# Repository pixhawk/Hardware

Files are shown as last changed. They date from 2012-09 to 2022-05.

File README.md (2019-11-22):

# Pixhawk Hardware Designs

 

[Pixhawk](http://pixhawk.org) is an independent open-hardware project that aims to provide "the gold standard" for readily-available, hiqh-quality and low-cost autopilot hardware designs for the academic, hobby and developer communities.
Pixhawk supports multiple flight stacks: PX4 ® and ArduPilot ®.

> **Note** Designs are provided for a number of components used in unmanned vehicles, including: Autopilots (Flight Management Units - FMUs), ESCs (electronic speed controllers), optical flow sensors, etc.

## What are Open Hardware Designs?

The [Pixhawk project](https://pixhawk.org/) provides open hardware designs following the [OSHW 1.1 definition](https://www.oshwa.org/definition/).

In essence, this definition allows anyone to freely study, modify, distribute, make, and sell the designs (or hardware based on the designs) under the terms of a particular [open source licence](#licensing).

## Hardware Designs

Hardware designs delivered by the project are listed below.

<span id="fmu_designs"></span>
### FMU (Autopilot) Designs

Pixhawk FMU open designs include all information required to create an autopilot hardware product that is *firmware compatible* with other hardware created from the same design.
Manufacturers are encouraged to take the designs and create products that are best suited to a particular market or use case (e.g. for very small vehicles, or those that operate at environmental extremes).

> **Note** While a physical connector standard is not mandated, newer products generally follow the [Pixhawk Connector Standard](https://pixhawk.org/pixhawk-connector-standard/).

#### Design Specifications

Designs are *usually* specified in the form of *schematics* that show all included components (CPU, sensors, etc.), how they are connected, and their pin mappings.
They may also include a BOM (bill of materials).

> **Note** Not all designs deliver schematics.
  A minimal design needs to contain enough information for manufacturers to create a compatible products; this can also be achieved using a precise pinout definition and information about connections of internal/external busses, etc.

#### Open Reference Hardware

The project provides *open reference hardware/layouts* for **some** open designs, in some versions.
These are provided in the form of PCB layout files.

The reference hardware files are shared under the same [license](#licenses) as the associated open design, and hence may be used in the same way(s).

#### FMU Versions

The Pixhawk project has evolved the FMU design through a number of verisons.

These are named using the designation: FMUvX (e.g.: FMUv1, FMUv2, FMUv3, FMUv4, etc.).
Higher FMU numbers indicate that the board is more recent, but may not indicate increased capability (versions can be almost identical - differing only in connector wiring).

The versions are listed below (with a high level overview of the main differences).

Version | Year | Lead Product | CPU | Other
--- | --- | --- | --- | ---
[FMUv1](FMUv1/README.md) & [IOv1](IOv1) | 2012 | None | 168 MHz M4 | (Discontinued) Original Flight Management Unit and Separate I/O board.
[FMUv2](FMUv2/README.md) | 2013 | Pixhawk 1 | 168 MHz M4 | Single board with STM32427VI processor.
[FMUv3](FMUv3_REV_D/README.md) | 2015 | Pixhawk 2 | 168 MHz M4 | Redundant sensors. Identical to FMUv2, but usable flash doubled to 2MB.
[FMUv4](FMUv4/README.md) | 2015 | Pixracer | 168 MHz M4 | Increased RAM. Faster CPU. More serial ports. No IO processor.
FMUv4X | 2017 | Pixhawk 3 Pro | 168 MHz M4 | Slightly increased RAM. More serial ports. IO processor. Redundant sensors.
[FMUv5](FMUv5/README.md) | 2018 | Pixhawk 4 | 200 MHz M7 | New processor (F7). Much faster. More RAM. More CAN busses. Much more configurable.<br>> **Note** Minimum specification provided (pinout info, but no schematics).
FMUv5X | 2019 | Pixhawk 5X | 200 MHz M7 | Temp-calibrated, redundant sensors.

> **Note** Products based on Pixhawk designs are listed here: [PX4 User Guide > Pixhawk Series]( https://docs.px4.io/master/en/flight_controller/pixhawk_series.html#pixhawk-series).

#### Derived FMU Products

Commercial products that are *derived* (under the terms of the open source license) from the Pixhawk FMU designs must provide their schematics and other information.

Relevant products are listed below:

- [MindPX V2 Hardware](MindPXv2/README.md)

### Sapog ESC

- [Sapog ESC](https://github.com/PX4/sapog) Hardware - The directory [sapog_reference_hardware](sapog_reference_hardware/README.md) contains the reference hardware design for the Sapog ESC firmware.

### Other

- [AIRSPEEDv1](AIRSPEEDv1) - 
- [FLOWv1](FLOWv1)
- [IMUv3_REV_C](IMUv3_REV_C)
- [PSMv3_REV_C](PSMv3_REV_C)

<span id="dev_call"></span>
## Dev Call

Pixhawk standards are developed in a weekly public developer call.

The call is shown in the [Dronecode calendar](https://www.dronecode.org/calendar/) as: *Pixhawk Hardware Standards Weekly Call* (all call details are in the entry).

<span id="licensing"></span>
## Licensing and Trademarks

Pixhawk project schematics and reference designs are licensed under [CC BY-SA 3](https://creativecommons.org/licenses/by-sa/3.0/legalcode).

The license allows you to use, sell, share, modify and build on the files in almost any way you like - provided that you give credit/attribution, and that you share any changes that you make under the same open source license (see the [human readable version of the license](https://creativecommons.org/licenses/by-sa/3.0/) for a concise summary of the rights and obligations).

> **Note** Boards that are *derived directly* from Pixhawk schematic files (or reference boards) must be open sourced.
  They can't be commercially licensed as proprietary products.

Manufacturers can create (compatible) *fully independent products* by first generating fresh schematic files that have the same pin mapping/components as the FMU designs.
Products that are based on independently created schematics are considered original works, and can be licensed as required.

<span id="trademarks"></span>
## Trademarks

The term *Pixhawk* is a trademark, and may not be used in product names without explicit permission from the trademark owner.

Typically this trademark is granted to the first board based on a particular FMU design and/or boards that use Pixhawk open reference hardware layouts.

> **Note** A "Pixhawk" is an autopilot that has been been given permission to use the Pixhawk trademark in its name.
  While other boards are based on the "Pixhawk FMU Standard", the are not *strictly speaking* "Pixhawks".

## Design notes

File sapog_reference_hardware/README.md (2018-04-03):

# Reference Hardware for PX4 Sapog



This directory contains the reference hardware design for
[PX4 Sapog](https://kb.zubax.com/x/cYAh) - an advanced open source ESC firmware.

This specific design is intended as an application note;
the main knowledge to gather from this design is the pinout of the MCU and its immediate connections.
The design is implemented in Eagle, version 7 or newer is required.

## Resources

* **[HOMEPAGE](https://kb.zubax.com/x/cYAh)**
* **[SUPPORT & FEEDBACK](https://forum.zubax.com/)**
* **[FIRMWARE ON GITHUB](https://github.com/PX4/sapog)**

## Design guidelines

1. When choosing the power transistors, keep their dynamic characteristics in mind:
the switching time must be under 50 nanoseconds.
Sapog employs somewhat unorthodox methods of state estimation which require a high-speed inverter.
2. The RC filters in the phase voltage feedback circuits should be designed so that their cutoff frequency
is around 19 kHz and the output impedance does not exceed 8 kohm.
3. Unless your maximum supply voltage exceeds 25 V (6S), do not change the DC link voltage measurement divider.

## License

The design is distributed under the terms of the
Creative Commons Attribution-ShareAlike 3.0 Unported license (CC BY-SA 3.0).

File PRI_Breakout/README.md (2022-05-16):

# Pixhawk Radio Interface (PRI) Breakout Board

> **General information about Pixhawk designs, schematics, reference hardware, FMU versions, licensing, and trademarks, and contributing to the project can be found in the repo [README](../README.md).**

This folder contains the design files for the PRI breakout board which splits the PRI connector into a power in, ethernet, usb and serial port. Documentation about the PRI standard can be found [here](https://github.com/pixhawk/Pixhawk-Standards).

## Design Files

The design is provided in [Altium Designer](https://www.altium.com/) CAD files.

It consists of schematic files (*.SchDoc), BOM listings, and includes open reference hardware PCB layouts (.PrjPcb). 

> **Tip** PDF versions of the schematics and PCB layouts has been made available for easy previewing (i.e. if you don't have Altium Designer).

<span id="licensing"></span>
## Licensing and Trademarks

The PRI breakout board design files are contributed by Auterion AG and licensed under [CC BY-SA 3](https://creativecommons.org/licenses/by-sa/3.0/legalcode).

The license allows you to use, sell, share, modify and build on the files in almost any way you like - provided that you give credit/attribution, and that you share any changes that you make under the same open source license (see the [human readable version of the license](https://creativecommons.org/licenses/by-sa/3.0/) for a concise summary of the rights and obligations).

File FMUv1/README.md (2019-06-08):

# FMUv1 Pixhawk Open Hardware Design

> **General information about Pixhawk designs, schematics, reference hardware, FMU versions, licensing, and trademarks, and contributing to the project can be found in the repo [README](../README.md).**

This is the first Pixhawk FMU design, and was intended to be used with various piggyback boards, including an [IO](IOv1) board (the boards were combined into one package for the FMUv2 design).

> **Warning** This design is end-of-life.

## Design Files

The design is provided in [EAGLE](https://www.autodesk.com/products/eagle/overview) CAD files (can be viewed with the free version).

It consists of schematic files (*.sch) and includes open reference hardware PCB layouts (.brd). 
BOM management is performed using [Bob Starr's BOM-EX plugin](http://www.bobstarr.net/pages/downloads.html).

## Feature Overview

The PX4-FMU (Flight Management Unit).
- Cortex M4F micro-controller and flash memory for controlling flight and communications.
- SD memory card socket
- 3 axis gyro for determining attitude/orientation.
- 3 axis accelerometer.
- Compass (magnetometer).
- Barometric pressure sensor (altitude)
- Connection for external UBLOX LEA GPS
- Interconnections for adding stackable peripheral boards.
- USB, JTAG and Serial interfaces/connections.
- PPM-SUM RC radio inputs
- Servo outputs.

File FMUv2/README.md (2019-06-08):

# FMUv2 Pixhawk Open Hardware Design

> **General information about Pixhawk designs, schematics, reference hardware, FMU versions, licensing, and trademarks, and contributing to the project can be found in the repo [README](../README.md).**

FMUv2 combines the FMUv1 and I/O designs into a single package.
The open design provides both schematics and open reference layouts.

## Design Files

The design is provided in [EAGLE](https://www.autodesk.com/products/eagle/overview) CAD files (can be viewed with the free version).

It consists of schematic files (*.sch) and includes open reference hardware PCB layouts (.brd). 
BOM management is performed using [Bob Starr's BOM-EX plugin](http://www.bobstarr.net/pages/downloads.html).

> **Tip** A PDF version of the schematics and PCB layouts has been made available for easy previewing: [PX4FMUv2.4.5.pdf](PX4FMUv2.4.5.pdf).

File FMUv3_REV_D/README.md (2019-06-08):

# FMUv3 Pixhawk Open Hardware Design

> **General information about Pixhawk designs, schematics, reference hardware, FMU versions, licensing, and trademarks, and contributing to the project can be found in the repo [README](../README.md).**

FMUv3 was introduced in 2015. Identical to FMUv2, it doubled the usable flash to 2MB.

The FMUv3 design is used in the Pixhawk 2 FC board.
This hardware is the result of a collaboration of the open hardware development community and 3D Robotics.

## Design Files

The design is provided in [Altium Designer](https://www.altium.com/) CAD files.

It consists of schematic files (*.SchDoc), BOM listings, and includes open reference hardware PCB layouts (.PrjPcb). 

> **Tip** PDF versions of the schematics and PCB layouts has been made available for easy previewing (i.e. if you don't have Altium Designer).

<!-- Removed text: FMUv3 open design (along with IMUv3 + PSMv3 support components) -->

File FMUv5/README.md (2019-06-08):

# FMUv5 Pixhawk Open Hardware Design

> **General information about Pixhawk designs, schematics, reference hardware, FMU versions, licensing, and trademarks, and contributing to the project can be found in the repo [README](../README.md).**

FMUv5 was released in 2018. When compared to previous versions it has a new processor, 2xRAM, new sensors with higher temperature stability, and is much more configurable. 
More information can be found in the [Pixhawk4 Data Sheet](Pixhawk4-Data-Sheet.pdf).

## Design Files

The FMUv5 reference design pinout is available [on Google docs here](https://docs.google.com/spreadsheets/d/1-n0__BYDedQrc_2NHqBenG1DNepAgnHpSGglke-QQwY/edit#gid=912976165) (linked from [FMUv5_stm32_pinout.md](FMUv5_stm32_pinout.md)).
This includes everything needed to create compatible hardware.

Note
- Schematics are not provided.
- Open reference hardware designs are not provided (Pixhawk 4 is a *proprietary* hardware layout based on this design).

## Other Files

This design additionally contains Pixhawk 4 information that may be useful if creating compatible products:
- [Pixhawk4 Pinouts](Pixhawk4-Pinouts.pdf)
- [Pixhawk4 Data Sheet](Pixhawk4-Data-Sheet.pdf)

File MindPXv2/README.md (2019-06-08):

# MindPX V2 Hardware

http://www.mindpx.net

MindPX V2.8 board

Product brief:
http://www.mindpx.net/assets/accessories/brochure.pdf

Hardware specification:
http://www.mindpx.net/assets/accessories/Specification_MindPX.pdf

User manual:
http://www.mindpx.net/assets/accessories/UserGuide_MindPX.pdf

Key features of v2.8:

1. 8 main PWM outputs + 8 aux PWM outputs
2. Dual-redundancy IMU components (onboard HMC5883L compass)
3. Support PPM/SBUS/SPEKTRUM DSM/Satellite RC input
4. Support FrSky/Wifi telemetry
5. One extra I2C port (so can support external compass and px4flow simultaneously)
6. Secondary USB port  for companion computer (converted from UART2 using onboard CP2104)
7. nrf/SPI port for SPI devices
8. exposed SWD debug port
9. Built-in vibration dampening for isolated IMU, support hard mount on air frames.
10. LTC2875 as CAN controller (+/- 60V overvoltage fault protection)

MindRacer V1.2 board (Hardware version: v1.2)

MindRacer specification:
http://mindpx.net/assets/accessories/mindracer_spec_v1.2.pdf

MindRacer user manual:
http://mindpx.net/assets/accessories/mindracer_user_guide_v1.2.pdf

Key features of v1.2:

1. 35 x 35mm (30.5 mm mounting holes) ultra mini size, weighs about 6g
2. STM32F427 as processor
3. 6 main PWM outputs
4. onboard MPU6500 & HMC5883L
5. dual 2x7 stackable header pins for I/O port replication/expansion
6. optional IMU isolation mounting support
7. Support PPM/SBUS/SPEKTRUM DSM/Satellite RC input
8. Support FrSky/Wifi telemetry
9. Onboard RTC battery and TF card slot
10. DroneCode standard connectors

Note: MindPX v2.8 & MindRacer v1.2 share same firmware.

## Licensing & Trademarks

Information on licensing and trademarks for Pixhawk designs can be found here: [Pixhawk Licensing](../README.md#license)

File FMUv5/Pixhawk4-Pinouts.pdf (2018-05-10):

## Pinouts

TELEM1, TELEM2 ports

Pin | Signal | Volt
1(red) | VCC | +5V
2(yellow) | TX(out) | +3.3V
3(blue) | RX(in) | +3.3V
4(white) | CTS(in) | +3.3V
5(green) | RTS(out) | +3.3V
6(black) | GND | GND

UART & I2C B port *

Pin | Signal | Volt
1(red) | VCC | +5V
2(yellow) | TX(out) | +3.3V
3(blue) | RX(in) | +3.3V
4(white) | SCL2 | +3.3V
5(green) | SDA2 | +3.3V
6(black) | GND | GND
*A spare port for connecting sensors supporting serial communication or I2C e.g. a second GPS module can be connected here.

DSM/SBUS RC port

Pin | Signal | Volt
1(red) | VDD_5V_SBUS_RC | +5V
2(yellow) | SBUS* | +3.3V
3(blue) | RSSI** | +3.3V
4(white) | VDD_3V3_SPEKTRUM | +3.3V
5(black) | GND | GND

*Connect SBUS or DSM/Spektrum receiver’s signal wire connect here. ** Sends the RC signal strength info to autopilot.

CAP & ADC IN port

Pin | Signal | Volt
1(red) | VCC | +5V
2 black) | FMU_CAP1 | +3.3V
3(black) | FMU_CAP2 | +3.3V
4(black) | FMU_CAP3 | +3.3V
5(black) | TIM5_SPARE_4 | +3.3V
6(black) | ADC1_SPARE_1 | +3.3V*
7(black) | ADC1_SPARE_2 | +6.6V*
8(black) | GND | GND
*WARNING: Sensors connected to this pin should not send a signal exceeding this voltage!

GPS port

Pin | Signal | Volt
1(red) | VCC | +5V
2 black) | TX(out) | +3.3V
3(black) | RX(in) | +3.3V
4(black) | SCL1 | +3.3V

5(black) | SDA1 | +3.3V
6(black) | SAFETY_SWITCH | +3.3V
7(black) | SAFETY_SWITCH_LED | +3.3V
8(black) | VDD_3V3 | +3.3V
9(black) | BUZZER | +5V
10(black) | GND | GND

FMU PWM OUT port

Pin | Signal | Volt
1(red) | VDD_SERVO
2 black) | FMU_CH1 | +3.3V
3(black) | FMU_CH2 | +3.3V
4(black) | FMU_CH3 | +3.3V
5(black) | FMU_CH4 | +3.3V
6(black) | FMU_CH5 | +3.3V
7(black) | FMU_CH6 | +3.3V
8(black) | FMU_CH7 | +3.3V
9(black) | FMU_CH8 | +3.3V
10(black) | GND | GND

I2C A port

Pin | Signal | Volt
1(red) | VCC | +5V
2(yellow) | SCL4 | +3.3V
3(blue) | SDA4 | +3.3V
4(black) | GND | GND

PPM RC port

Pin | Signal | Volt
1(red) | VCC | +5V
2(yellow) | PPM | +3.3V
3(black) | GND | GND

SPI port

Pin | Signal | Volt
1(red) | VCC | +5V
2 (black) | SCK | +3.3V
3(black) | MISO | +3.3V
4(black) | MOSI | +3.3V
5(black) | CS1 | +3.3V
6(black) | CS2 | +3.3V
7(black) | GND | GND

Power 1, Power 2 ports

Pin | Signal | Volt
1(red) | VCC | +5V
2(yellow) | VCC | +5V
3(blue) | CURRENT | +3.3V
4(white) | VOLTAGE | +3.3V
5(green) | GND | GND
6(black) | GND | GND

USB port

Pin | Signal | Volt
1(red) | VBUS | +5V
2(yellow) | DM | +3.3V
3(blue) | DP | +3.3V
4(black) | GND | GND

CAN1, CAN2 ports

Pin | Signal | Volt
1(red) | VCC | +5V
2(yellow) | CANH | +3.3V
3(blue) | CANL | +3.3V
4(black) | GND | GND

SBUS OUT port

Pin | Signal | Volt

1(red)

2(yellow) | SBUS_OUT | +3.3V
3(black) | GND | GND

I/O PWM OUT port

Pin | Signal | Volt
1(red) | VDD_SERVO
2 black) | IO_CH1 | +3.3V
3(black) | IO_CH2 | +3.3V
4(black) | IO_CH3 | +3.3V
5(black) | IO_CH4 | +3.3V

6(black) | IO_CH5 | +3.3V
7(black) | IO_CH6 | +3.3V
8(black) | IO_CH7 | +3.3V
9(black) | IO_CH8 | +3.3V
10(black) | GND | GND

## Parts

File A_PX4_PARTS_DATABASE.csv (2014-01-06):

Mfg Part Num | Mfg Name | VID | Vendor Part Num | Description | Vendor Qty 1 | Vendor Qty 2 | Vendor Qty 3 | Customer Ref | Price Qty 1 | Price Qty 2 | Price Qty 3 | Vendor Reel Part Num | Vendor Link | Datasheet Link | VID2 | Vendor 2 Part Num | Vendor 2 Derivate Part Num | Vendor 2 Price Qty 1 | Vendor 2 Link
CC0402ZRY5V7BB104 | Yageo | DK | 311-1047-1-ND | CAP .10UF 16V CERAMIC Y5V 0402 | 10 | 100 | 500 |  | 0.011 | 0.0065 | 0.00376 | 311-1047-6-ND | http://search.digikey.com/scripts/DkSearch/dksus.dll?Detail&name=311-1047-1-ND | http://media.digikey.com/pdf/Data%20Sheets/Yageo%20PDFs/MLCC%20ordering%20code.pdf | ME | 81-GRM155R71C104KA88 | GRM155R71C104KA88D | 0.022 | http://at.mouser.com/ProductDetail/Murata/GRM155R71C104KA88D/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
F931A106MAA | Nichicon | DK | 493-2351-1-ND | CAP TANTALUM 10UF 10V 20% SMD | 10 | 100 | 250 |  | 0.349 | 0.21 | 0.15752 | 493-2351-6-ND | http://search.digikey.com/scripts/DkSearch/dksus.dll?Detail&name=493-2351-1-ND | http://products.nichicon.co.jp/en/pdf/XJA039/e-f93.pdf | ME | 80-B45196H2106K109 | B45196H2106K109 | 0.203 | http://at.mouser.com/ProductDetail/Kemet/B45196H2106K109/?qs=sGAEpiMZZMuEN2agSAc2pkTaD7b2aQjmQy5HG6VoQ2g%3d
MSS1P4-M3/89A | Vishay | DK | MSS1P4-M3/89AGICT-ND | DIODE SCHOTTKY 1A 40V MICROSMP | 10 | 100 | 250 |  | 0.326 | 0.1919 | 0.13576 | MSS1P4-M3/89AGIDKR-ND | http://search.digikey.com/scripts/DkSearch/dksus.dll?Detail&name=MSS1P4-M3/89AGICT-ND | http://www.vishay.com/docs/89019/mss1p4.pdf | ME | 625-MSS1P4-M3 | MSS1P4-M3/89A | 0.245 | http://at.mouser.com/ProductDetail/Vishay/MSS1P4-M3-89A/?qs=fLSHF8TigmUkO6GnwlXAxQ%3d%3d
953230-2000-AR-PR | 3M | DK | 3M9272CT-ND | CONN SOCKET 30POS 2MM VERT SMD | 1 | 100 |  |  | 3.22 | 2.449 |  | 3M9272DKR-ND | http://search.digikey.com/scripts/DkSearch/dksus.dll?Detail&name=3M9272CT-ND | http://multimedia.3m.com/mws/mediawebserver?mwsId=66666UuZjcFSLXTtmXMEm8T_EVuQEcuZgVs6EVs6E666666-- | ME | 517-953230-2000-ARPR | 953230-2000-AR-PR | 3.35 | http://at.mouser.com/ProductDetail/3M-Electronic-Solutions-Division/953230-2000-AR-TP/
47346-0001 | Molex Inc | DK | WM17141CT-ND | CONN RCPT 5POS MICRO USB R/A | 10 | 50 | 250 |  | 0.793 | 0.6612 | 0.54992 | WM17141DKR-ND | http://search.digikey.com/scripts/DkSearch/dksus.dll?Detail&name=WM17141DKR-ND | http://www.molex.com/pdm_docs/sd/473460001_sd.pdf | ME | 538-47346-0001 | 47346-0001 | 1.44 | http://at.mouser.com/ProductDetail/Molex/47346-0001/?qs=c2CV6XM0DweJBWaSeyWeCw%3d%3d
M50-3900542 | Harwin Inc | DK | 952-1395-ND | CONN HDR 1.27MM R/A AU 10POS | 10 | 50 | 100 |  | 1.242 | 1.035 | 0.92 |  | http://search.digikey.com/scripts/DkSearch/dksus.dll?vendor=0&keywords=M50-3900542 | http://www.harwin.com/include/downloads/pdfs/2010PAGE95.PDF | ME | 855-M50-3900542 | M50-3900542 | 0.968 | http://at.mouser.com/ProductDetail/Harwin/M50-3900542/?qs=9fQaSFfsqsyxvSF9FxJVZQ%3d%3d
L3G4200DH | STMicroelectronics | DK | 497-11071-1-ND | IC GYROSCOPE MEMS 3AXIS LP 16LGA | 10 | 100 | 250 |  | 12.39 | 10.62 | 9.73500 | 497-11071-6-ND | http://search.digikey.com/scripts/DkSearch/dksus.dll?Detail&name=497-11071-1-ND | http://www.st.com/stonline/products/literature/ds/17116.pdf | ME | 511-L3G4200D | L3G4200D | 12.41 | http://at.mouser.com/ProductDetail/STMicroelectronics/L3G4200D/?qs=sGAEpiMZZMtlZAfbtrLey%252by4mKX%2fvdEL
HMC5843 | HMC5843 | DK | 342-1071-1-ND | SENSOR MAGNETIC 3 AXIS 20-LCC | 1 | 100 | 500 |  | 20 | 17 | 15 | 342-1071-6-ND | http://search.digikey.com/scripts/DkSearch/dksus.dll?Detail&name=342-1071-1-ND | http://www.sparkfun.com/datasheets/Sensors/Magneto/HMC5843.pdf
BMP0805 | Bosch Sensortec | DK | 828-1005-1-ND | DIGITAL BAROMETRIC PRESSURE SNSR | 10 | 100 | 250 |  | 8.79 | 7.325 | 5.567 | 828-1005-6-ND | http://search.digikey.com/scripts/DkSearch/dksus.dll?Detail&name=828-1005-1-ND | http://www.bosch-sensortec.com/content/language1/downloads/BST-BMP085-DS000-05.pdf
LIS331DLH | STMicroelectronics | DK | 497-10397-1-ND | ACCELEROMETER MEMS 3AXIS 16-LGA | 10 | 100 | 250 |  | 8.316 | 6.93 | 6.237 | 497-10397-6-ND | http://search.digikey.com/scripts/DkSearch/dksus.dll?Detail&name=497-10397-1-ND | http://www.st.com/internet/com/TECHNICAL_RESOURCES/TECHNICAL_LITERATURE/DATASHEET/CD00213470.pdf | ME | 511-LIS331DLH | LIS331DLH | 7.87 | http://at.mouser.com/ProductDetail/STMicroelectronics/LIS331DLH/?qs=sGAEpiMZZMvAvBNgSS9Lql%252bnfyR4OMMz
24FC128-I/MS | Microchip | DK | 24FC128-I/MS-ND | IC EEPROM 128KBIT 1MHZ 8MSOP | 10 | 25 | 100 |  | 0.84 | 0.6 | 0.58 |  | http://search.digikey.com/scripts/DkSearch/dksus.dll?Detail&name=24FC128-I/MS-ND | http://ww1.microchip.com/downloads/en/DeviceDoc/21191s.pdf | ME | 579-24FC128-I/MS | 24FC128-I/MS | 0.639 | http://at.mouser.com/ProductDetail/Microchip/24FC128-I-MS/?qs=XNV0BZVlaZHXU0%2fvkIaqxQ%3d%3d
7M-16.000MEEQ-T | TXC | DK | 887-1319-1-ND | CRYSTAL 16.000 MHZ 10PF SMD | 10 | 50 | 100 |  | 1.463 | 1.2826 | 1.0125 | 887-1319-6-ND | http://search.digikey.com/scripts/DkSearch/dksus.dll?Detail&name=887-1319-1-ND | http://www.txccrystal.com/images/pdf/7m-accuracy.pdf | ME | 717-7M-16.000MEEQ-T | 7M-16.000MEEQ-T | 9999 | http://at.mouser.com/ProductDetail/TXC/7M-16000MEEQ-T/?qs=65dIHZNch5syu%2fvH9aFnbA%3d%3d
MIC5207-3.3YM5 | Micrel Inc | DK | 576-1267-1-ND | IC REG LDO 180MA 3.3V SOT23-5 | 1 | 100 | 250 |  | 1.02 | 0.85 | 0.51 | 576-1267-6-ND | http://search.digikey.com/scripts/DkSearch/dksus.dll?Detail&name=576-1267-1-ND | http://www.micrel.com/_PDF/mic5207.pdf
LD1117AS33 | STMicroelectronics | DK | 497-1228-1-ND | IC REG LDO 3.3V 1.2A SOT-223 | 10 | 100 | 250 |  | 0.84 | 0.663 | 0.5746 | 497-1228-6-ND | http://search.digikey.com/scripts/DkSearch/dksus.dll?Detail&name=497-1228-1-ND | http://www.st.com/internet/com/TECHNICAL_RESOURCES/TECHNICAL_LITERATURE/DATASHEET/CD00002116.pdf | ME | 511-LD1117AS33 | LD1117AS33TR | 0.477 | http://at.mouser.com/ProductDetail/STMicroelectronics/LD1117AS33TR/?qs=C3bf%2fVrkE5CoDDd7wyn%252baQ%3d%3d
EVQP7J01K | Panasonic - ECG | DK | P12278SCT-ND | SWITCH LT 3.5MMX2.9MM 160GF SMD | 10 | 100 | 500 |  | 0.734 | 0.6163 | 0.52826 | P12278SDKR-ND | http://search.digikey.com/scripts/DkSearch/dksus.dll?Detail&name=P12278SCT-ND | http://industrial.panasonic.com/www-data/pdf/ATK0000/ATK0000CE20.pdf
SN74LVC2T45 | Texas Instruments | DK | 296-17014-1-ND | Translator, Bidirectional, 3-State, 2bits | 1 | 25 | 100 |  | 0.79 | 0.612 | 0.54 | 296-17014-6-ND | http://search.digikey.com/scripts/DkSearch/dksus.dll?Detail&name=296-17014-1-ND | http://focus.ti.com/lit/ds/symlink/sn74lvc2t45.pdf | ME | 595-SN74LVC2T45DCUR | SN74LVC2T45DCUR | 0.766 | http://at.mouser.com/ProductDetail/Texas-Instruments/SN74LVC2T45DCUR/?qs=0smPjiIwnfIdG9vxyJHBdA%3d%3d
BKP1005HS121-T | Taiyo Yuden | DK | 587-1921-1-ND | FERRITE BEAD 120 OHM 0402 | 10 | 100 | 500 |  | 0.2 | 0.08 | 0.041 | 587-1921-6-ND | http://search.digikey.com/scripts/DkSearch/dksus.dll?Detail&name=587-1921-1-ND | http://www.yuden.co.jp/us/product/pdf/ebkp_e.pdf | ME | 81-BLM15PD121SN1D | BLM15PD121SN1D | 0.107 | http://at.mouser.com/ProductDetail/Murata/BLM15PD121SN1D/
BM06B-SRSS-TB | JST | DK | 455-1792-1-ND | CONN HEADER SH 6POS TOP 1MM TIN | 10 | 100 | 500 |  | 0.66 | 0.5504 | 0.4403 | 455-1792-6-ND | http://search.digikey.com/scripts/DkSearch/dksus.dll?Detail&name=455-1792-1-ND | http://www.jst-mfg.com/product/pdf/eng/eSH.pdf
GRM155F51C474ZA01D | Murata Electronics | DK | 490-3274-1-ND | CAP CER .47UF 16V Y5V 0402 | 10 | 100 | 500 |  | 0.044 | 0.026 | 0.015 | 490-3274-6-ND | http://search.digikey.com/scripts/DkSearch/dksus.dll?Detail&name=490-3274-1-ND | http://search.murata.co.jp/Ceramy/image/img/PDF/ENG/GRM155F51C474ZA01.pdf
53261-15 | Molex Inc | DK | WM7632CT-ND | CONN HEADER 15POS 1.25MM R/A SMD | 10 | 50 | 100 |  | 2.199 | 1.8992 | 1.6993 | WM7632DKR-ND | http://search.digikey.com/scripts/DkSearch/dksus.dll?Detail&name=WM7632CT-ND | http://www.molex.com/pdm_docs/sd/532611571_sd.pdf | ME | 538-53261-1571 | 53261-1571 | 3.79 | http://at.mouser.com/ProductDetail/Molex/53261-1571/?qs=sGAEpiMZZMticT%2fTNjssTkTynroYBL5J
CC0402KRX7R7BB103 | Yageo | DK | 311-1042-1-ND | CAP 10000PF 16V CERAMIC X7R 0402 | 10 | 100 | 500 |  | 0.011 | 0.0067 | 0.00386 | 311-1042-6-ND | http://search.digikey.com/scripts/DkSearch/dksus.dll?Detail&name=311-1042-1-ND | http://media.digikey.com/pdf/Data%20Sheets/Yageo%20PDFs/MLCC%20ordering%20code.pdf | ME | 810-C1005X7R1C103K | C1005X7R1C103K | 0.032 | http://at.mouser.com/ProductDetail/TDK/C1005X7R1C103K/?qs=sGAEpiMZZMvQvaS66kI3ToxS7c2J4e237rb4UXwcIBM%3d
C1005Y5V1C224Z | TDK Corporation | DK | 445-3444-1-ND | CAP CER .22UF 16V Y5V 0402 | 10 | 100 | 500 |  | 0.03 | 0.0176 | 0.01012 | 445-3444-6-ND | http://search.digikey.com/scripts/DkSearch/dksus.dll?Detail&name=445-3444-1-ND | http://www.tdk.com/pdf/general_A11.pdf
C1608Y5V0J475Z | TDK Corporation | DK | 445-3449-1-ND | CAP CER 4.7UF 6.3V Y5V 0603 | 10 | 100 | 500 |  | 0.121 | 0.0715 | 0.04126 | 445-3449-6-ND | http://search.digikey.com/scripts/DkSearch/dksus.dll?Detail&name=445-3449-1-ND | http://www.tdk.com/pdf/general_A11.pdf | ME | 810-C1608X5R0J475M | C1608X5R0J475M | 0.095 | http://at.mouser.com/ProductDetail/TDK/C1608X5R0J475M/
CC0402KRX7R9BB471 | Yageo | DK | 311-1028-1-ND | CAP 470PF 50V CERAMIC X7R 0402 | 10 | 100 | 500 |  | 0.011 | 0.0067 | 0.00386 | 311-1028-6-ND | http://search.digikey.com/scripts/DkSearch/dksus.dll?Detail&name=311-1028-1-ND | http://media.digikey.com/pdf/Data%20Sheets/Yageo%20PDFs/MLCC%20ordering%20code.pdf
TXB0102DCUR | Texas Instruments | DK | 296-22862-1-ND | IC VOLT-LVL TRANSL BI-DIR 8-US8 | 1 | 25 | 100 |  | 1.48 | 1.17 | 1.053 | 296-22862-6-ND | http://search.digikey.com/scripts/DkSearch/dksus.dll?Detail&name=296-22862-1-ND | http://focus.ti.com/lit/ds/symlink/txb0102.pdf | ME | 595-TXB0102DCUR | TXB0102DCUR | 1.55 | http://at.mouser.com/ProductDetail/Texas-Instruments/TXB0102DCUR/
MF-FSMF050X-2 | Bourns Inc. | DK | MF-FSMF050X-2CT-ND | FUSE PTC RESET 500MA SMD 0603 | 10 | 100 | 500 |  | 0.36 | 0.33 | 0.312 | MF-FSMF050X-2DKR-ND | http://search.digikey.com/scripts/DkSearch/dksus.dll?Detail&name=MF-FSMF050X-2CT-ND | http://www.bourns.com/data/global/pdfs/mffsmf.pdf | ME | 652-MFFSMF050X-2 | MF-FSMF050X-2 | 0.448 | http://at.mouser.com/ProductDetail/Bourns/MF-FSMF050X-2/?qs=3QkGRBNOvbrZekaW8Gqm4A%3d%3d
MF-FSMF020X-2 | Bourns Inc. | DK | MF-FSMF020X-2CT-ND | FUSE PTC RESET 200MA SMD 0603 | 10 | 100 | 500 |  | 0.36 | 0.33 | 0.312 | MF-FSMF020X-2DKR-ND | http://search.digikey.com/scripts/DkSearch/dksus.dll?Detail&name=MF-FSMF020X-2CT-ND | http://www.bourns.com/data/global/pdfs/mffsmf.pdf | ME | 652-MFFSMF020X-2 | MF-FSMF020X-2 | 0.448 | http://at.mouser.com/ProductDetail/Bourns/MF-FSMF020X-2/?qs=3QkGRBNOvbqaTWjqPUQNsg%3d%3d
C1608Y5V1C225Z | TDK Corporation | DK | 445-3451-1-ND | CAP CER 2.2UF 16V Y5V 0603 | 10 | 100 | 500 |  | 0.088 | 0.052 | 0.03 | 445-3451-6-ND | http://search.digikey.com/scripts/DkSearch/dksus.dll?Detail&name=445-3451-1-ND | http://www.tdk.com/pdf/general_A11.pdf | ME | 810-C1608Y5V1C225Z | C1608Y5V1C225Z | 0.085 | http://at.mouser.com/ProductDetail/TDK/C1608Y5V1C225Z/
CC0402JRNP09BN100 | Yageo | DK | 311-1014-1-ND | CAP CERAMIC 10PF 50V NP0 0402 | 10 | 100 | 500 |  | 0.012 | 0.007 | 0.00406 | 311-1014-6-ND | http://search.digikey.com/scripts/DkSearch/dksus.dll?Detail&name=311-1014-1-ND | http://www.yageo.com/documents/recent/UPY-GP_NP0_16V-to-50V_6.pdf | ME | 581-04023U100JAT2A | 04023U100JAT2A | 0.032 | http://at.mouser.com/ProductDetail/AVX/04023U100JAT2A/
RC0402FR-0739K2L | Yageo | DK | 311-39.2KLRCT-ND | RES 39.2K OHM 1/16W 1% 0402 SMD | 10 | 50 | 200 |  | 0.067 | 0.0362 | 0.02085 | 311-39.2KLRDKR-ND | http://search.digikey.com/scripts/DkSearch/dksus.dll?Detail&name=311-39.2KLRCT-ND | http://www.yageo.com/documents/recent/PYu-RC0402_51_RoHS_L_6.pdf | ME | 304-39.2K-RC | 304-39.2K-RC | 0.045 | http://at.mouser.com/ProductDetail/Xicon/304-392K-RC/?qs=sGAEpiMZZMtG0KNrPCHnjZ81IsZ41qnEdwGMvS7VK3o%3d
ERJ-2GEJ680X | Panasonic - ECG | DK | P68JCT-ND | RES 68 OHM 1/10W 5% 0402 SMD | 1 | 50 | 100 |  | 0.05 | 0.0172 | 0.0131 | P68JDKR-ND | http://search.digikey.com/scripts/DkSearch/dksus.dll?Detail&name=P68JCT-ND | http://industrial.panasonic.com/www-cgi/jvcr13pz.cgi?E+PZ+3+AOA0001+ERJ2GEJ680X+7+WW
CC0402ZRY5V7BB104 | TDK | ME | 810-C1005X7R1C104M | CAP .10UF 16V CERAMIC Y7R 0402 | 10 | 100 | 500 |  | 0.032 | 0.01 | 0.009 | 810-C1005X7R1C104M | http://at.mouser.com/ProductDetail/TDK/C1005X7R1C104M/?qs=sGAEpiMZZMvQvaS66kI3Ts8kcYAvnUrc2X3P8fTRlAY%3d | http://media.digikey.com/pdf/Data%20Sheets/Yageo%20PDFs/MLCC%20ordering%20code.pdf
SM06B-SRSS-TB | JST | DK | 455-1806-1-ND | CONN HEADER SH 6POS SIDE 1MM TIN | 10 | 100 | 500 |  | 0.653 | 0.5445 | 0.4356 | 455-1806-6-ND | http://search.digikey.com/scripts/DkSearch/dksus.dll?Detail&name=455-1806-1-ND | http://www.jst-mfg.com/product/pdf/eng/eSH.pdf
ABM3B-8.000MHZ-10-1-U-T | Abracon Corporation | DK | 535-9721-1-ND | CRYSTAL 8.000 MHZ 10PF SMD | 10 | 50 | 100 |  | 2.048 | 1.7956 | 1.4175 | 535-9721-6-ND | http://search.digikey.com/scripts/DkSearch/dksus.dll?Detail&name=535-9721-1-ND | http://www.abracon.com/Resonators/abm3b.pdf | ME | 815-ABM3B-8.0-B2-T | ABM3B-8.000MHZ-B2-T | 1.01 | http://at.mouser.com/ProductDetail/ABRACON/ABM3B-8000MHZ-B2-T/?qs=NE97hfUNX0Ef9OqIOqO2cA%3d%3d
STM32F100C6T6B | STMicroelectronics | DK | 497-10500-ND | MCU 32BIT ARM 32K FLASH 48LQFP | 10 | 100 | 250 |  | 2.55 | 2.091 | 1.887 |  | http://search.digikey.com/scripts/DkSearch/dksus.dll?Detail&name=497-10500-ND | http://www.st.com/internet/com/TECHNICAL_RESOURCES/TECHNICAL_LITERATURE/DATASHEET/CD00251732.pdf | ME | 511-STM32F100C6T6B | STM32F100C6T6B | 2.77 | http://at.mouser.com/ProductDetail/STMicroelectronics/STM32F100C6T6B/?qs=sGAEpiMZZMs%2f2%2fdgfKIueKwtjHOoM53O
PTH08080WAH | Texas Instruments | DK | 296-20432-ND | MODULE PIP .9-5.5V 2.25A HORZ TH | 1 | 25 | 100 |  | 10.75 | 8.8152 | 7.955 |  | http://search.digikey.com/scripts/DkSearch/dksus.dll?vendor=0&keywords=PTH08080WAH&stock=1 | http://focus.ti.com/lit/ds/symlink/pth08080w.pdf | ME | 595-PTH08080WAH | PTH08080WAH | 11.3 | http://at.mouser.com/ProductDetail/Texas-Instruments/PTH08080WAH/?qs=sGAEpiMZZMuo%252bmZx5g6tFE82QReiwhO7
53047-02 | Molex Inc | DK | WM1731-ND | CONN HEADER 2POS 1.25MM VERT TIN | 50 | 100 | 250 |  | 0.2778 | 0.2395 | 0.21076 |  | http://search.digikey.com/scripts/DkSearch/dksus.dll?WT.z_header=search_go&lang=en&site=us&x=0&y=0 | http://www.molex.com/pdm_docs/sd/530470210_sd.pdf
53047-03 | Molex Inc | DK | WM1732-ND | CONN HEADER 3POS 1.25MM VERT TIN | 50 | 100 | 250 |  | 0.342 | 0.2948 | 0.2594 |  | http://search.digikey.com/scripts/DkSearch/dksus.dll?WT.z_header=search_go&lang=en&site=us&x=0&y=0 | http://www.molex.com/pdm_docs/sd/530470310_sd.pdf
53047-04 | Molex Inc | DK | WM1733-ND | CONN HEADER 4POS 1.25MM VERT TIN | 50 | 100 | 250 |  | 0.378 | 0.329 | 0.28 |  | http://search.digikey.com/scripts/DkSearch/dksus.dll?WT.z_header=search_go&lang=en&site=us&x=0&y=0 | http://www.molex.com/pdm_docs/sd/530470410_sd.pdf
53047-05 | Molex Inc | DK | WM1734-ND | CONN HEADER 5POS 1.25MM VERT TIN | 50 | 100 | 250 |  | 0.4816 | 0.4192 | 0.3568 |  | http://search.digikey.com/scripts/DkSearch/dksus.dll?WT.z_header=search_go&lang=en&site=us&x=0&y=0 | http://www.molex.com/pdm_docs/sd/530470510_sd.pdf
T491X107K025ZT | Kemet | DK | 399-5175-1-ND | CAP TANT 100UF 25V 10% SMD | 10 | 25 | 100 |  | 2.453 | 2.3448 | 2.1645 | 399-5175-6-ND | http://search.digikey.com/scripts/DkSearch/dksus.dll?Detail&name=399-5175-1-ND | http://www.kemet.com/datasheets&T491X107K025ZT
T491A475K010AT | Kemet | DK | 399-3696-1-ND | CAPACITOR TANT 4.7UF 10V 10% SMD | 10 | 100 | 250 |  | 0.349 | 0.21 | 0.15752 | 399-3696-6-ND | http://search.digikey.com/scripts/DkSearch/dksus.dll?Detail&name=399-3696-1-ND | http://www.kemet.com/datasheets&T491A475K010AT
TC164-JR-07100RL | Yageo | DK | TC164J-100CT-ND | RES ARRAY 100 OHM 8TRM 4 RES SMD | 10 | 100 | 500 |  | 0.012 | 0.0103 | 0.00736 | TC164J-100DKR-ND | http://search.digikey.com/scripts/DkSearch/dksus.dll?Detail&name=TC164J-100CT-ND | http://www.yageo.com/documents/recent/PYu-YC_TC164_51_RoHS_L_3.pdf
SN74LVC8T245DBQR | Texas Instruments | DK | 296-23279-1-ND | IC BUS TRANSCVR 8BIT 24QSOP | 1 | 25 | 100 |  | 1.33 | 1.05 | 0.945 | 296-23279-6-ND | http://search.digikey.com/scripts/DkSearch/dksus.dll?Detail&name=296-23279-1-ND | http://focus.ti.com/lit/ds/symlink/sn74lvc8t245.pdf
S3B-ZR-SM4A-TF | JST | DK | 455-1694-1-ND | CONN HEADER ZH SIDE 3POS 1.5MM | 1 | 10 | 100 |  | 0.56 | 0.516 | 0.43 | 455-1694-6-ND | http://search.digikey.com/scripts/DkSearch/dksus.dll?Detail&name=455-1694-1-ND
TLP3123(F) | Toshiba | DK | TLP3123F-ND | PHOTORELAY MOSFET 1A 4-SOP | 10 | 100 | 250 |  | 3.15 | 2.45 | 2.32752 |  | http://search.digikey.com/scripts/DkSearch/dksus.dll?WT.z_header=search_go&lang=en&site=us&x=0&y=0 | http://www.semicon.toshiba.co.jp/docs/datasheet/en/Opto/TLP3123_en_datasheet_071001.pdf
AP2151WG-7 | Diodes Inc | DK | AP2151WGDICT-ND | IC PWR SW USB 1CH 0.5A SOT-25-5 | 10 | 100 | 250 |  | 0.855 | 0.675 | 0.585 |  | http://search.digikey.com/scripts/DkSearch/dksus.dll?Detail&name=AP2151WGDICT-ND | http://www.diodes.com/datasheets/AP2141_51.pdf
74LVC2GU04GW,125 | NXP Semiconductors | DK | 568-4843-1-ND | IC DUAL INVERTER SC88-6 | 1 | 25 | 100 |  | 0.52 | 0.3428 | 0.2816 | 568-4843-6-ND | http://search.digikey.com/scripts/DkSearch/dksus.dll?Detail&name=568-4843-1-ND | http://www.nxp.com/documents/data_sheet/74LVC2GU04.pdf | ME | 771-LVC2GU04GW125 | 74LVC2GU04GW,125 | 0.577 | http://ch.mouser.com:80/Search/ProductDetail.aspx
MAX3051ESA+ | Maxim Integrated Products | DK | MAX3051ESA+-ND | IC TXRX CAN 1MBPS 8-SOIC | 1 | 25 | 100 |  | 2.56 | 1.71 | 1.24 |  | http://search.digikey.com/scripts/DkSearch/dksus.dll?Detail&name=MAX3051ESA%2B-ND | http://datasheets.maxim-ic.com/en/ds/MAX3051.pdf
DF12C(3.0)-50DS-0.5V | Hirose Electric Co Ltd | DK | DF12C(3.0)-50DS-0.5V(81)-ND | CONN RECEPT 50 POS SMD 0.5MM | 1000 |  |  |  | 0.8379 |  |  |  | http://search.digikey.com/scripts/DkSearch/dksus.dll?WT.z_header=search_go&lang=en&site=us&x=0&y=0 | http://www.hirose.co.jp/cataloge_hp/e53700036.pdf
B4B-PH-K | JST | DK | 455-1706-ND | CONN HEADER PH TOP 4POS 2MM | 10 | 100 | 500 |  | 0.11122 | 0.167 | 0.139 |  | http://search.digikey.com/scripts/DkSearch/dksus.dll?vendor=0&keywords=B4B-PH-K-S&stock=1 | http://www.jst-mfg.com/product/pdf/eng/ePH.pdf
S02B-PASK-2 | JST | DK | 455-1847-ND | CONN HEADER PA 2POS SIDE 2MM TIN | 10 | 100 | 500 |  | 0.225 | 0.1872 | 0.14974 |  | http://search.digikey.com/scripts/DkSearch/dksus.dll?vendor=0&keywords=S02B-PASK-2&stock=1 | http://www.jst-mfg.com/product/pdf/eng/ePA-F.pdf
B3B-ZR | JST | DK | 455-1658-ND | CONN HEADER ZH TOP 3POS 1.5MM | 10 | 100 | 500 |  | 0.123 | 0.1028 | 0.08222 | 455-1682-6-ND | http://search.digikey.com/scripts/DkSearch/dksus.dll?Detail&name=455-1658-ND | http://www.jst-mfg.com/product/pdf/eng/eZH.pdf
53261-03 | Molex Inc | DK | WM7621CT-ND | CONN HEADER 3POS 1.25MM R/A SMD | 10 | 50 | 100 |  | 1.09 | 0.9082 | 0.8173 | WM7621DKR-ND | http://search.digikey.com/scripts/DkSearch/dksus.dll?Detail&name=WM7621CT-ND | http://www.molex.com/pdm_docs/sd/532610371_sd.pdf
53261-04 | Molex Inc | DK | WM7622CT-ND | CONN HEADER 4POS 1.25MM R/A SMD | 10 | 50 | 100 |  | 1.193 | 0.994 | 0.8946 | WM7622DKR-ND | http://search.digikey.com/scripts/DkSearch/dksus.dll?Detail&name=WM7622CT-ND | http://www.molex.com/pdm_docs/sd/532610471_sd.pdf
P120JCT-ND | Panasonic - ECG | DK | P120JCT-ND | RES 120 OHM 1/10W 5% 0402 SMD | 1 | 50 | 100 |  | 0.05 | 0.0172 | 0.0131 | P120JDKR-ND | http://search.digikey.com/scripts/DkSearch/dksus.dll?Detail&name=P120JCT-ND | http://industrial.panasonic.com/www-cgi/jvcr13pz.cgi?E+PZ+3+AOA0001+ERJ2GEJ121X+7+WW
ERJ-2RKF3570X | Panasonic - ECG | DK | P357LCT-ND | RES 357 OHM 1/10W 1% 0402 SMD | 1 | 50 | 100 |  | 0.06 | 0.0242 | 0.0184 | P357LDKR-ND | http://search.digikey.com/scripts/DkSearch/dksus.dll?Detail&name=P357LCT-ND | http://industrial.panasonic.com/www-cgi/jvcr13pz.cgi?E+PZ+3+AOA0002+ERJ2RKF3570X+7+WW
AMIS42673ICAG1RG | ON Semiconductor | DK | 766-1008-1-ND | TRANSCEIVER CAN HS 3.3V 8-SOIC | 1 | 100 | 250 |  | 2.38 | 1.666 | 1.496 | 766-1008-6-ND | http://search.digikey.com/scripts/DkSearch/dksus.dll?Detail&name=766-1008-1-ND | http://www.onsemi.com/pub_link/Collateral/AMIS-42673-D.PDF
STM32F103C4T6A | STMicroelectronics | DK | 497-8316-ND | MCU ARM 32BIT 16K FLASH 48-LQFP | 10 | 100 | 250 |  | 5.85 | 4.81 | 4.42 |  | http://search.digikey.com/scripts/DkSearch/dksus.dll?Detail&name=497-8316-ND | http://www.st.com/internet/com/TECHNICAL_RESOURCES/TECHNICAL_LITERATURE/DATASHEET/CD00210843.pdf
STM32F102C6T6A | STMicroelectronics | DK | 497-8306-ND | MCU ARM 32BIT 32KB FLASH 48-LQFP | 10 | 100 | 250 |  | 5.67 | 4.662 | 4.284 |  | http://search.digikey.com/scripts/DkSearch/dksus.dll?Detail&name=497-8306-ND | http://www.st.com/internet/com/TECHNICAL_RESOURCES/TECHNICAL_LITERATURE/DATASHEET/CD00210833.pdf
LNJ337W83RA | Panasonic - SSG | DK | LNJ337W83RACT-ND | LED GREEN HIGH BRIGHT ESS SMD | 1 | 25 | 100 |  | 0.53 | 0.31 | 0.25 | LNJ337W83RADKR-ND | http://search.digikey.com/scripts/DkSearch/dksus.dll?Detail&name=LNJ337W83RACT-ND | http://industrial.panasonic.com/www-cgi/jvcr13pz.cgi?E+SC+4+ATA7003+LNJ337W83RA+8+WW
HMC5883L | Honeywell | DK | 342-1082-1-ND | IC COMPASS 3 AXIS I2C 16LCC SMD | 1 | 25 | 100 |  | 3.79 | 2.2356 | 1.8829 | 342-1082-6-ND | http://search.digikey.com/scripts/DkSearch/dksus.dll?Detail&name=342-1082-1-ND | http://media.digikey.com/PDF/Data%20Sheets/Honeywell%20PDFs/HMC5883L.pdf
STM32F205 | STMicroelectronics | DK | 497-11157-ND | MCU ARM 1024KB FLASH 64LQFP | 1 | 25 | 100 |  | 15.38 | 12.9316 | 11.883 |  | http://search.digikey.com/scripts/DkSearch/dksus.dll?lang=en&site=US&KeyWords=stm32f205rgt6&x=0&y=0 | http://www.st.com/internet/com/TECHNICAL_RESOURCES/TECHNICAL_LITERATURE/DATASHEET/CD00237391.pdf
951230-2520-AR-PR | 3M | DK | 3M9197CT-ND | CONN HEADER 30POS 2MM VERT SMD | 1 | 100 |  |  | 2.2 | 1.6748 |  |  | http://search.digikey.com/scripts/DkSearch/dksus.dll?Detail&name=3M9197CT-ND | http://multimedia.3m.com/mws/mediawebserver?66666UuZjcFSLXTtmxTXmXfEEVuQEcuZgVs6EVs6E666666-- | ME | 538-87759-3050 | 87759-3050 | 5.4 | http://ch.mouser.com:80/ProductDetail/Molex/87759-3050/?qs=sGAEpiMZZMtsLRyDR9nM10M7wAK5dulTwNabOIeF5lA%3d
ERJ-2RKF2050X | Panasonic - ECG | DK | P205LCT-ND | RES 205 OHM 1/10W 1% 0402 SMD | 1 | 50 | 100 |  | 0.06 | 0.0242 | 0.0184 | P205LDKR-ND | http://search.digikey.com/scripts/DkSearch/dksus.dll?Detail&name=P205LCT-ND | http://industrial.panasonic.com/www-cgi/jvcr13pz.cgi?E+PZ+3+AOA0002+ERJ2RKF2050X+7+WW
NTGS4111P | ON Semiconductor | DK | NTGS4111PT1G | MOSFET P-CH 30V 2.6A 6-TSOP | 10 | 100 | 250 |  | 0.445 | 0.3042 | 0.25352 | NTGS4111PT1GOSDKR-ND | http://search.digikey.com/scripts/DkSearch/dksus.dll?Detail&name=NTGS4111PT1GOSCT-ND | http://www.onsemi.com/pub_link/Collateral/NTGS4111P-D.PDF
NX3225SA-24.000000MHZ | NDK | DK | NX3225SA-24.000000MHZ | CRYSTAL 24.000000 MHZ 8PF SMD | 10 | 50 | 100 |  | 0.92 | 0.8064 | 0.6367 | 644-1052-6-ND | http://search.digikey.com/scripts/DkSearch/dksus.dll?Detail&name=644-1052-1-ND | http://media.digikey.com/pdf/Data%20Sheets/NDK%20PDFs/NX3225SA.pdf | ME | 815-ABM8G-24-18-D2Y | ABM8G-24.000MHZ-18-D2Y-T | 1.79 | http://at.mouser.com:80/ProductDetail/ABRACON/ABM8G-24000MHZ-18-D2Y-T/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
FT4232HL | FTDI | DK | 768-1026-1-ND | IC USB HS QUAD UART/SYNC 64-LQFP | 10 | 50 | 100 |  | 8.66 | 8.1 | 6.84 | 768-1026-6-ND | http://search.digikey.com/scripts/DkSearch/dksus.dll?Detail&name=768-1026-1-ND | http://www.ftdichip.com/Support/Documents/DataSheets/ICs/DS_FT4232H.pdf
7M-12.000MEEQ-T | TXC CORPORATION | DK | 887-1316-1-ND | CRYSTAL 12.000 MHZ 10PF SMD | 10 | 50 | 100 |  | 1.463 | 1.2826 | 1.0125 | 887-1316-6-ND | http://search.digikey.com/scripts/DkSearch/dksus.dll?Detail&name=887-1316-1-ND | http://www.txccrystal.com/images/pdf/7m-accuracy.pdf
MMS1208 | APEM Components, LLC | DK | 679-1854-ND | SWITCH MICRO-MINI SLIDE | 10 | 50 | 100 |  | 1.003 | 0.85 | 0.765 |  | http://search.digikey.com/scripts/DkSearch/dksus.dll?WT.z_header=search_go&lang=en&site=us&x=0&y=0 | http://www.apem.com/pdf/MMS_MICRO_SLIDE.pdf
TS3A24157 | Texas Instruments | DK | 296-22856-1-ND | IC SWITCH DUAL SPDT 10MSOP | 1 | 25 | 100 |  | 1.41 | 1.11 | 0.999 | 296-22856-6-ND | http://search.digikey.com/scripts/DkSearch/dksus.dll?Detail&name=296-22856-1-ND | http://focus.ti.com/lit/ds/symlink/ts3a24157.pdf
UX60SC-MB-5ST(80) | Hirose Electric Co Ltd | DK | H11671CT-ND | CONN RCPT USB MINI B R/A SMD | 10 | 25 | 100 |  | 0.62 | 0.55 | 0.45 | H11671DKR-ND | http://search.digikey.com/scripts/DkSearch/dksus.dll?Detail&name=H11671CT-ND | http://www.hirose.co.jp/cataloge_hp/e24000153.pdf
EVQ-5PN04K | Panasonic - ECG | DK | P13595SCT-ND | SWITCH LT TOUCH 6X3.5 240GF SMD | 10 | 100 | 500 |  | 0.513 | 0.4309 | 0.36936 | P13595SDKR-ND | http://search.digikey.com/scripts/DkSearch/dksus.dll?Detail&name=P13595SCT-ND | http://industrial.panasonic.com/www-data/pdf/ATK0000/ATK0000CE7.pdf
SBH11-PBPC-D10-RA-BK | Sullins Connector Solutions | DK | S9180-ND | CONN HEADR 2.54MM 20POS GOLD R/A | 1 | 25 | 100 |  | 0.76 | 0.6888 | 0.4879 |  | http://search.digikey.com/scripts/DkSearch/dksus.dll?Detail&name=S9180-ND | http://www.sullinscorp.com/drawings/145_SBH11-PBPC-D___-RA-___,_11092-B.pdf
XG4C-3031 | Omron Electronics Inc-EMC Div | DK | OR994-ND | CONN PLUG 30POS 3A 300V STRT DIP | 1 | 25 | 100 |  | 1.61 | 1.4468 | 1.1576 |  | http://search.digikey.com/scripts/DkSearch/dksus.dll?Detail&name=OR994-ND | http://components.omron.com/components/web/pdflib.nsf/0/1D642D622E2FDCF685257201007DD590/$file/XG4_1110.pdf
68000-406HLF | FCI | DK | 609-3263-ND | CONN HEADER 6POS .100 STR TIN | 1 | 25 | 100 |  | 0.37 | 0.1744 | 0.1352 |  | http://search.digikey.com/scripts/DkSearch/dksus.dll?Detail&name=609-3263-ND | http://portal.fciconnect.com/res/en/pdffiles/doc_search/68000.pdf
93LC46BT-I/ST | Microchip Technology | DK | 93LC46BT-I/STCT-ND | IC EEPROM 1KBIT 2MHZ 8TSSOP | 10 | 25 | 100 |  | 0.26 | 0.25 | 0.24 | 93LC46BT-I/STDKR-ND | http://search.digikey.com/scripts/DkSearch/dksus.dll?Detail&name=93LC46BT-I/STCT-ND | http://ww1.microchip.com/downloads/en/DeviceDoc/21749H.pdf
TXS0102DCUR | Texas Instruments | DK | 296-21931-1-ND | IC VOLT-LEVEL TRANSLATOR 8-US8 | 1 | 25 | 100 |  | 1.25 | 0.99 | 0.891 | 296-21931-6-ND | http://search.digikey.com/scripts/DkSearch/dksus.dll?Detail&name=296-21931-1-ND | http://focus.ti.com/lit/ds/symlink/txs0102.pdf
STM32F100C8T6B | STMicroelectronics | DK | 497-10499-ND | MCU 32BIT ARM 64K FLASH 48LQFP | 10 | 100 | 250 |  | 3.425 | 2.8085 | 2.53452 |  | http://search.digikey.com/scripts/DkSearch/dksus.dll?Detail&name=497-10499-ND | http://www.st.com/internet/com/TECHNICAL_RESOURCES/TECHNICAL_LITERATURE/DATASHEET/CD00251732.pdf
BAT 60A E6327 | Infineon Technologies | DK | BAT60AE6327INCT-ND | DIODE SCHOTTKY 10V 3A SOD-323 | 10 | 100 | 500 |  | 0.38300 | 0.25550 | 0.14820 | BAT60AE6327INDKR-ND | http://search.digikey.com/scripts/DkSearch/dksus.dll?Detail&name=BAT60AE6327INCT-ND | http://www.infineon.com/dgdl/bat60aseries.pdf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
BLM15HD102SN1 | Murata Electronics | DK | 490-4003-1-ND | FILTER CHIP 1000 OHM 250MA 0402 | 10 | 50 | 100 |  | 0.41500 | 0.27340 | 0.21680 | 490-4003-6-ND | http://search.digikey.com/scripts/DkSearch/dksus.dll?Detail&name=490-4003-1-ND | http://search.murata.co.jp/Ceramy/image/img/PDF/ENG/L0110S0101BLM15H.pdf
STM32F405RGT6 | STMicroelectronics | DK | 497-11767-ND | IC MCU 168 MHZ FPU 32BIT 1MB FLASH 64LQFP | 10 | 100 | 250 |  | 13.08800 | 11.12460 | 10.14300 |  | http://search.digikey.com/us/en/products/STM32F405RGT6/497-11767-ND/2754208 | http://www.st.com/internet/com/TECHNICAL_RESOURCES/TECHNICAL_LITERATURE/DATASHEET/DM00037051.pdf
RC0402FR-0747KL | Yageo | DK | 311-47.0KLRCT-ND | RES 47.0K OHM 1/16W 1% 0402 SMD | 10 | 50 | 100 |  | 0.01400 | 0.01040 | 0.00790 | 311-47.0KLRDKR-ND | http://search.digikey.com/us/en/products/RC0402FR-0747KL/311-47.0KLRCT-ND/729563 | http://www.yageo.com/documents/recent/PYu-RC0402_51_RoHS_L_6.pdf
DF13-3P-1.25H(20) | Hirose Electric Co Ltd | DK | H2220-ND | CONN HEADER 3POS 1.25MM R/A TIN | 10 | 50 | 1000 |  | 0.49000 | 0.37800 | 0.18900 |  | http://search.digikey.com/us/en/products/DF13-3P-1.25H(20)/H2220-ND/241793 | http://www.hirose.co.jp/cataloge_hp/e53600014.pdf
DF13-2P-1.25DSA | Hirose Electric Co Ltd | DK | H2191-ND | CONN HEADER 2POS 1.25MM STR TIN | 10 | 50 | 1000 |  | 0.31300 | 0.20880 | 0.10080 |  | http://search.digikey.com/us/en/products/DF13-2P-1.25DSA/H2191-ND/241765 | http://www.hirose.co.jp/cataloge_hp/e53600014.pdf
DF13-4P-1.25DSA | Hirose Electric Co Ltd | DK | H2193-ND | CONN HEADER 4POS 1.25MM STR TIN | 10 | 50 | 1000 |  | 0.39900 | 0.30780 | 0.15390 |  | http://search.digikey.com/us/en/products/DF13-4P-1.25DSA/H2193-ND/241767 | http://www.hirose.co.jp/cataloge_hp/e53600014.pdf
DF13-4P-1.25H(20) | Hirose Electric Co Ltd | DK | H2221-ND | CONN HEADER 4POS 1.25MM R/A TIN | 10 | 50 | 1000 |  | 0.52700 | 0.42500 | 0.22610 | DF13-4P-1.25H(21)-ND | http://search.digikey.com/us/en/products/DF13-4P-1.25H(20)/H2221-ND/241794 | http://www.hirose.co.jp/cataloge_hp/e53600014.pdf
DF13-3P-1.25DSA | Hirose Electric Co Ltd | DK | H2192-ND | CONN HEADER 3POS 1.25MM STR TIN | 10 | 50 | 1000 |  | 0.30500 | 0.23500 | 0.11745 |  | http://search.digikey.com/us/en/products/DF13-3P-1.25DSA/H2192-ND/241766 | http://www.hirose.co.jp/cataloge_hp/e53600014.pdf
DF13A-3P-1.25H(20) | Hirose Electric Co Ltd | DK | H3368-ND | CONN HEADER 3POS 1.25MM R/A TIN | 10 | 50 | 1000 |  | 0.49000 | 0.37800 | 0.18900 |  | http://search.digikey.com/us/en/products/DF13A-3P-1.25H(20)/H3368-ND/530665 | http://www.hirose.co.jp/cataloge_hp/e53600014.pdf
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

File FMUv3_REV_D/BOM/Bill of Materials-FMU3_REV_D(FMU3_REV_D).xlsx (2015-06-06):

Manufacturer 1 | Manufacturer Part Number 1 | Description | Designator | Value | Quantity | Footprint
Yageo | CC0402ZRY5V7BB104 | CAP CER 0.1UF 16V Y5V 0402 | C1001, C3001, C3002, C3003, C3004, C4003, C4005, C4006, C5001, C5005, C5007, C5009, C5010, C5011, C5012, C5014, C5015, C7001, C7002, C7003, C7006, C8001, C8002, C8003, C10002 | 0u1 | 25 | 0402-CAP
TDK Corporation | C1005C0G1H080C050BA | CAP CER 8PF 50V C0G 0402 | C1002, C1003, C7004, C7005 | 8p | 4 | 0402-CAP
TDK Corporation | C1608X6S1C225K080AC | CAP CER 2.2UF 16V 10% X6S 0603 | C4001, C4002, C5013, C5016 | 2u2 | 4 | 0603-CAP
AVX Corporation | 06033C103JAT2A | CAP CER 10000PF 25V 5% X7R 0603 | C4004 | 0u01 | 1 | 0603-CAP
TDK Corporation | C1005X6S1E224K050BC | CAP CER 0.22UF 25V 10% X7R 0402 | C4007 | 0u22 | 1 | 0402-CAP
Samsung Electro-Mechanics America, Inc | CL21B475KOFNNNE | CAP CER 4.7UF 16V 10% X7R 0805 | C4008 | 4u7 | 1 | 0805
Samsung Electro-Mechanics America, Inc | CL21A106KAYNNNE | CAP CER 10UF 25V 10% X5R 0805 | C5002, C10001 | 10u/25 | 2 | 0805-CAP
Yageo | CC0402KRX7R7BB103 | CAP CER 10000PF 16V 10% X7R 0402 | C5003, C10003 | 10n | 2 | 0402-CAP
Yageo | CC0603ZRY5V7BB105 | CAP CER 1UF 16V Y5V 0603 | C5004, C10005 | 1u | 2 | 0603-CAP
Samsung Electro-Mechanics America, Inc | CL21A226MAQNNNE | CAP CER 22UF 25V 20% X5R 0805 | C5006, C5008 | 22u/25V | 2 | 0805-CAP
Murata Electronics North America | GRM21BR60G107ME15L |  | C5100, C5101 | 100uF | 2 | C0805
TDK Corporation | C1608X5R1A106K080AC | CAP CER 10UF 10V 10% X5R 0603 | C10004 | 10u | 1 | 0603-CAP
ON Semiconductor | RB751V40T1G | DIODE SCHOTTKY 30V 0.03A SOD323 | D5001 | 30V | 1 | SOD323
TE Connectivity / Raychem | PESD0402-140 | TVS DIODE 14VWM 40VC 0402 | D8001, D8002 | 40v | 2 | 0402-TVS
NXP Semiconductors | PMEG2005CT,215 | DIODE SCHOTTKY 20V 500MA TO236AB | D10001 | 20V | 1 | SOT23-3
Bel Fuse Inc | 0ZCA0035FF2G | PTC RESTTBLE 0.35A 16V CHIP 1206 | F10001 | 0.35A | 1 | PTC-1206
Molex Inc | 0473460001 | MICRO USB B, BOTTOM MOUNT | J2001 |  | 1 | MOLEX-47346-0001
AVX Corp/Kyocera Corp | KNH16C104DA5TS | FILTER CAP 0.1UF 2A 25V 0603 | L2001, L2002, L5001 | 0u1 | 3 | KYOCERA-KNH16-DA
Kingbright | APTD1608CGCK | LED GREEN ROUND CLEAR SMD | LED1, LED2, LED6001, LED6002, LED6003, LED6004, LED6005, LED6006, LED6007, LED6008, LED6009 | GREEN | 11 | 0603-LED-Blue
Kingbright | APTD1608SECK/J4-PF | LED 1.6X0.8 DOME ORN CLEAR SMD | LED6010, LED6011 | AMBER | 2 | 0603-LED
Infineon Technologies | MMBT 3906 LT1 | TRANSISTOR SWITCHING PNP SOT-23 | Q5001 |  | 1 | SOT23-BEC
Diodes Incorporated | BSS123-7-F | MOSFET N-CH 100V 170MA SOT23-3 | Q6001 | 100V | 1 | SOT23
Yageo | RC0402FR-07220RL | RES 220 OHM 1/16W 1% 0402 SMD | R1, R2, R1022, R4001, R4002, R6003, R6004, R6005, R6006, R6007, R6008, R6009, R6010, R6011, R6012, R6013, R6014, R6015, R7003, R7004, R7010, R7011, R7012 | 220R | 23 | 0402-RES
Yageo | RC0402FR-07470RL | RES 470 OHM 1/16W 1% 0402 SMD | R1001 | 470R | 1 | 0402-RES
Yageo | RC0402FR-0710KL | RES 10K OHM 1/16W 1% 0402 SMD | R1002, R5001, R5006, R6002, R7001, R7002, R8001 | 10K | 7 | 0402-RES
Panasonic Electronic Components | ERA-2AEB103X | RES 10K OHM 1/16W .1% 0402 SMD | R2001, R2002 | 10K | 2 | 0402-RES
Yageo | RC0402FR-071ML | RES 1M OHM 1/16W 1% 0402 SMD | R2003, R2004 | 1M | 2 | 0402-RES
Yageo | RC0402FR-071K5L | RES 1.5K OHM 1/16W 1% 0402 SMD | R3001, R3002, R3003, R3004, R6017 | 1K5 | 5 | 0402-RES
Yageo | RC0402FR-07120RL | RES 120 OHM 1/16W 1% 0402 SMD | R3005, R3006, R3007, R3008, R3009, R3010 | 120R | 6 | 0402-RES
Samsung Electro-Mechanics America, Inc | RC1005F182CS | RES 1.8K OHM 1/16W 1% 0402 | R5002 | 1K8 | 1 | 0402-RES
Samsung Electro-Mechanics America, Inc | RC1608J100CS | RES 10 OHM 1/10W 5% 0603 | R5003 | 10R | 1 | 0603-RES
Samsung Electro-Mechanics America, Inc | RC1005F102CS | RES 1K OHM 1/16W 1% 0402 | R5005, R6001 | 1K | 2 | 0402-RES
Panasonic | ERJ-2GEJ680X | Thick Film Resistors - SMD 0402 68ohms 5% Tol | R6016 | 68R | 1 | 0402-RES
Yageo | RC0402FR-07100KL | RES 100K OHM 1/16W 1% 0402 SMD | R10001 | 100K | 1 | 0402-RES
Panasonic Electronic Components | EXB-2HV104JV | RES ARRAY 100K OHM 8 RES 1506 | RN2001 | 100K | 1 | EXB2HV
Panasonic Electronic Components | EXB-2HV103JV | RES ARRAY 10K OHM 8 RES 1506 | RN2002 | 10K | 1 | EXB2HV
Panasonic Electronic Components | EXB-2HV121JV | RES ARRAY 120 OHM 8 RES 1506 | RN3001, RN3002, RN8001, RN8002 | 120R | 4 | EXB2HV
STMicroelectronics | STM32F427VIT6 | REV 3 Silicon or later IC MCU ARM 2MB FLASH 100LQFP | U1001 |  | 1 | TQFP100
Cypress Semiconductor Corp | FM25V01-G | IC FRAM 128KBIT 40MHZ 8SOIC | U1002 | 128k | 1 | SO08
ON Semiconductor | NUF2042XV6T1G | IC FILTER USB ESD PROTECT SOT363 | U2001 |  | 1 | SOT563-6
3M | 2908-05WB-MG | CONN MICRO SD CARD PUSH-PUSH R/A | U2002 |  | 1 | MICROSD
Texas Instruments | TXS0108ERGYR | IC XLATR VOLT-LVL 8B BDIR 20QFN | U3001, U3002, U8001, U8002 |  | 4 | QFN20-RGY
Maxim Integrated | MAX3051EKA+T | IC TXRX CAN 1MBPS SOT23-8 | U3003, U3004 | CAN | 2 | SOT23-8
InvenSense | MPU-6000 | GYRO/ACCELEROMETER 6AXIS 24QFN | U4001 |  | 1 | QFN-24
Honeywell Microelectronics & Precision Sensors | HMC5983-TR | IC COMPASS 3 AXIS 16-LCC | U4002 |  | 1 | HMC5983-new
Measurement Specialties, Inc. | MS561101BA03-50 | Board Mount Pressure Sensors | U4003 | 10-1200mbar | 1 | MS5611-01BA
Micrel Inc | MIC5332-SSYMT TR | IC REG LDO 3.3V 0.3A 8TMLF | U5001, U10002 | 3.3V | 2 | MLF-8-EPAD
STMicroelectronics | STM32F100C8T6B | MCU 32BIT ARM 64K FLASH 48LQFP | U7001 |  | 1 | TQFP48
NXP Semiconductors | 74LVC2G240DP,125 | IC INVERTER DUAL 4-INPUT 8TSSOP | U8003 | INV | 1 | TSSOP8_SOT505-2
Texas Instruments | BQ24313DSGT | IC LI+ CHARGER FRONT END 8-SON | U10001 |  | 1 | QFN8-DSG
Hirose Electric Co Ltd | DF40C(2.0)-20DS-0.4V(51) | CONN RCPT 20POS 0.4MM SMD GOLD | U$2 |  | 1 | DF-40C-20DS
Hirose Electric Co Ltd | DF17(3.0H)-80DS-0.5V(57) | CONN RECEPT 80POS .5MM SMD W/FIT | U$9001 |  | 1 | CON-DF17-80F
NDK | NX3225SA-24.000MHZ-STD-CSR-1 | CRYSTAL 24MHZ 8PF SMD | X1001, X7001 | 24MHz | 2 | OSCILLATOR-3.2X2.5

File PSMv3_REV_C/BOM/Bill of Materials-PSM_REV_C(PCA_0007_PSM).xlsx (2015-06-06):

Manufacturer 1 | Manufacturer Part Number 1 | Description | Designator | Value | Quantity | Footprint
Yageo | CC0402KRX7R7BB103 | CAP CER 10000PF 16V 10% X7R 0402 | C1 | 10N | 1 | 0402-CAP
Samsung Electro-Mechanics America, Inc | CL21A106KAYNNNE | CAP CER 10UF 25V 10% X5R 0805 | C2 | 10UF | 1 | 0805-CAP
Yageo | CC0603ZRY5V7BB105 | CAP CER 1UF 16V Y5V 0603 | C3, C7 | 1U | 2 | 0603-CAP
TDK Corporation | C1608X5R1A106K080AC | CAP CER 10UF 10V 10% X5R 0603 | C4, C401, C402 | 10U | 3 | 0603-CAP
Yageo | CC0402ZRY5V7BB104 | CAP CER 0.1UF 16V Y5V 0402 | C5 | 0U1 | 1 | 0402-CAP
TDK Corporation | C1005X5R1C474K050BC | CAP CER 0.47UF 16V 10% X5R 0402 | C6 | 0U47 | 1 | 0402-CAP
Kemet | C0402C562K5RACTU | CAP CER 5600PF 50V 10% X7R 0402 | C8 | 5N6 | 1 | 0402-CAP
TDK Corporation | C3216X5R1A107M160AC | CAP CER 100UF 10V 20% X5R 1206 | C801, C803, C805, C810 | 100U | 4 | 1206-CAP
Kemet | C0402C100J3GACTU | CAP CER 10PF 25V 5% NP0 0402 | C802, C804 | 10P | 2 | 0402-CAP
Murata Electronics North America | GRM1555C1E102JA01D | CAP CER 1000PF 25V 5% NP0 0402 | C806 | 1000P | 1 | 0402-CAP
TDK Corporation | C1005X7R1E104K050BB | CAP CER 0.1UF 25V 10% X7R 0402 | C807, C808, C809 | 0U1 | 3 | 0402-CAP
NXP Semiconductors | PMEG2005CT,215 | DIODE SCHOTTKY 20V 500MA TO236AB | D1, D3 | 20V | 2 | SOT23-3
ON Semiconductor | MMSZ5232BT1G | DIODE ZENER 5.6V 500MW SOD123 | D4 | 5.6V | 1 | SOD-123
Bel Fuse Inc | 0ZCA0035FF2G | PTC RESTTBLE 0.35A 16V CHIP 1206 | F1, F3 | 0.35A | 2 | PTC-1206
Bel Fuse Inc | 0ZCA0020FF2E | PTC RESTTBLE 0.20A 30V CHIP 1206 | F4 | 0.2A | 1 | PTC-1206
TDK Corporation | MLZ2012M470WTD25 | FIXED IND 47UH 170MA 4.81 OHM | L1 | 47UH | 1 | 0805-IND
AVX Corp/Kyocera Corp | KNH16C104DA5TS | FILTER CAP 0.1UF 2A 25V 0603 | L603 | 0U1 | 1 | KYOCERA-KNH16-DA
Micro Commercial Co | MMBT3906-TP | TRANS SS PNP 40V 300MW SOT23 | Q5001 | 40V | 1 | SOT23-BEC
Stackpole Electronics Inc | RMCF0402FT453K | RES 453K OHM 1/16W 1% 0402 | R1, R801, R804, R807 | 453K | 4 | 0402-RES
Stackpole Electronics Inc | RMCF0402FT16K5 | RES 16.5K OHM 1/16W 1% 0402 | R2, R401, R10001 | 16K5 | 3 | 0402-RES
Yageo | RC0402FR-07100KL | RES 100K OHM 1/16W 1% 0402 SMD | R3 | 100K | 1 | 0402-RES
Yageo | RC0402FR-0710KL | RES 10K OHM 1/16W 1% 0402 SMD | R4, R404 | 10K | 2 | 0402-RES
Stackpole Electronics Inc | RMCF0402FT9K09 | RES 9.09K OHM 1/16W 1% 0402 | R5 | 9K09 | 1 | 0402-RES
Yageo | RC0402FR-071ML | RES 1M OHM 1/16W 1% 0402 SMD | R402, R405 | 1M | 2 | 0402-RES
Stackpole Electronics Inc | RMCF0402FT25K5 | RES 25.5K OHM 1/16W 1% 0402 | R403 | 25K5 | 1 | 0402-RES
Panasonic Electronic Components | ERA-2AEB563X | RES 56K OHM 1/16W .1% 0402 SMD | R802, R805, R808 | 5.6K | 3 | 0402-RES
Panasonic Electronic Components | ERJ-2RKF1053X | RES 105K OHM 1/10W 1% 0402 SMD | R803, R806, R809 | 105K | 3 | 0402-RES
Samsung Electro-Mechanics America, Inc | RC1005F102CS | RES 1K OHM 1/16W 1% 0402 | R5002 | 1K | 1 | 0402-RES
Panasonic Electronic Components | EXB-28V105JX | RES ARRAY 1M OHM 4 RES 0804 | RN801 | 1M | 1 | EXB28V
Micrel Inc | MIC5332-SSYMT TR | IC REG LDO 3.3V 0.3A 8TMLF | U1 | 3.3V | 1 | MLF-8-EPAD
Linear Technology | LT3469ETS8#TRMPBF | IC AMP DVR W/REG 1.3MHZ TSOT23-8 | U2 | BUZZER | 1 | SOT23-8
Texas Instruments | BQ24315DSGT | IC LI+ CHARGER FRONT END 8SON | U401, U402 | 3.3V-30V | 2 | QFN8-DSG
ON Semiconductor | NTHD4102PT1G | MOSFET 2P-CH 20V 2.9A CHIPFET | U801, U802, U804 | 20V 2.9A | 3 | 1206-8
Linear Technology | LTC4417IUF#PBF | IC OR CTRLR SRC SELECT 24QFN | U803 | 3:1 | 1 | MO-220
Texas Instruments | BQ24313DSGT | IC LI+ CHARGER FRONT END 8-SON | U10001 | 3.3V-30V | 1 | QFN8-DSG
 |  |  |  | Total Qty. | 60
 |  |  |  | APPROVALS
PART NUMBER (3DR ERP) | BOM REVISION | REF. DRAWING/SCHEMATIC: |  | Dept. | Name | Signature
PCA_0007_PSM |  | PSM_REV_C.PrjPcb |  | Design Engineering (PR)
PRODUCT DESCRIPTION | ECR/ECO/ECN |  |  | Dir. Of Eng. | Tim M.
PSM_REV_C.PrjPcb |  | N/A |  | Operations Mgmt | Lorenzo L.
Total parts = | 60 | N/A |  | Production | Juan V.
Feeder requirement: | N/A | N/A

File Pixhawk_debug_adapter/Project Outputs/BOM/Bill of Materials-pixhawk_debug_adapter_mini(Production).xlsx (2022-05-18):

Line # | Name | Description | Designator | Quantity | Manufacturer 1 | Manufacturer Part Number 1 | Manufacturer Lifecycle 1 | Supplier 1 | Supplier Part Number 1 | Supplier Unit Price 1 | Supplier Subtotal 1
1 | MOUNT HOLE 3MM 8VIAS THMOUNT_HOLE_3MM_TH | MOUNT HOLE 3MM 8VIAS TH | M1, M2, M3, M4 | 4
2 | TESTPOINT MINIATURE SMD | TESTPOINT MINIATURE SMD | GND | 1 | Keystone Electronics | 5015 | Volume Production | Digi-Key | 36-5015CT-ND | 0.47 | 0.47
3 | CAP CER 0.1UF 10% 50V X5R 0402 | CAP CER 0.1UF 10% 50V X5R 0402 | C1 | 1 | Murata | GRM155R61H104KE19D | Volume Production | Digi-Key | 490-11917-1-ND | 0.11 | 0.11
4 | DIODE ZENER 5.1V 225MW SOT23-3 | DIODE ZENER 5.1V 225MW SOT23-3 | D1 | 1 | ON Semiconductor | BZX84C5V1LT3G | Volume Production | Digi-Key | BZX84C5V1LT3GOSCT-ND | 0.13 | 0.13
5 | DIODE SCHOTTKY 70V 70MA SOD523 | DIODE SCHOTTKY 70V 70MA SOD523 | D2 | 1 | STMicroelectronics | BAS70KFILM | Volume Production | Digi-Key | 497-5695-1-ND | 0.26 | 0.26
6 | CONN_HDR_2X10_VERT_SHROUD_FTSH_1.27MM_SMT | CONN_HDR_2X10_VERT_SHROUD_FTSH_1.27MM_SMT | J1 | 1 | Samtec | FTSH-110-01-L-DV-K-TR | Volume Production | Digi-Key | SAM13960CT-ND | 5.36 | 5.36
7 | CONN HEADER SUR 8POS .8MM VERT SMT | CONN HEADER SUR 8POS .8MM VERT SMT | J2 | 1 | JST | BM08B-SURS-TF(LF)(SN) | Not Recommended for New Design | Digi-Key | 455-3578-1-ND
8 | CONN_HDR_2X10_MALE_2.54MM_SHR_SAMTEC_SMD | CONN_HDR_2X10_MALE_2.54MM_SHR_SAMTEC_SMD | J3 | 1 | Samtec | HTST-110-01-L-DV | Volume Production | Digi-Key | SAM10529-ND | 2.6 | 2.6
9 | CONN HEADER SH 10POS TOP 1MM TIN | CONN HEADER SH 10POS TOP 1MM TIN | J4 | 1 | JST | BM10B-SRSS-TB(LF)(SN) | Volume Production | Digi-Key | 455-1796-1-ND
10 | CONN HEADER 10POS DUAL .05" SMD | CONN HEADER 10POS DUAL .05" SMD | J5 | 1 | Samtec | FTSH-105-01-F-DV-K | Volume Production | Digi-Key | SAM8796-ND
11 | CONN HEADER SH 6POS TOP 1MM TIN | CONN HEADER SH 6POS TOP 1MM TIN | J7 | 1 | JST | BM06B-SRSS-TBT(LF)(SN) | Volume Production | Digi-Key | 455-2875-1-ND | 1.01 | 1.01
12 | CONN HEADER 6POS 0.100" (2.54mm) SMD | CONN HEADER 6POS 0.100" (2.54mm) SMD | J9 | 1 | Samtec | TSM-106-01-L-SV-P-TR | Volume Production | Digi-Key | SAM14846CT-ND | 1.57 | 1.57
13 | JUMPER SHORTING BAR 2MM PAD | JUMPER SHORTING BAR 2MM PAD | JP1 | 1
14 | RES SMD 68 OHM 1% 1/8W 0805 | RES SMD 68 OHM 1% 1/8W 0805 | R1 | 1 | Yageo | RC0805FR-0768RL | Volume Production | Digi-Key | 311-68.0CRCT-ND | 0.1 | 0.1
15 | RES SMD 10K OHM 1% 1/16W 0402 | RES SMD 10K OHM 1% 1/16W 0402 | R2, R3 | 2 | Yageo | RC0402FR-0710KL | Volume Production | Digi-Key | 311-10.0KLRCT-ND
16 | RES SMD 100K OHM 1% 1/16W 0402 | RES SMD 100K OHM 1% 1/16W 0402 | R4 | 1 | Yageo | RC0402FR-07100KL | Volume Production | Digi-Key | 311-100KLRCT-ND | 0.1 | 0.1
17 | SWITCH TACTILE SPST-NO 0.05A 12V SMT | SWITCH TACTILE SPST-NO 0.05A 12V SMT | SW1 | 1 | E-Switch | TL3365AF180QG | Volume Production | Digi-Key | EG5384CT-ND | 0.32 | 0.32
18 | IC GATE AND 1CH 2-INP 5-TSOP | IC GATE AND 1CH 2-INP 5-TSOP | U1 | 1 | ON Semiconductor | MC74VHC1G09DTT1G | Volume Production | Digi-Key | MC74VHC1G09DTT1GOSCT-ND | 0.32 | 0.32

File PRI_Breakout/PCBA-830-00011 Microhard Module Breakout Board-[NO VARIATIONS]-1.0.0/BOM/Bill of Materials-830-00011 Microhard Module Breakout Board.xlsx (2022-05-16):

Name | Description | Designator | Manufacturer 1 | Manufacturer Part Number 1 | Supplier 1 | Supplier Part Number 1 | Quantity
UCM1V151MCL1GS | CAP ALUM 150UF 20% 35V SMD | C1 | Nichicon | UCM1V151MCL1GS |  |  | 1
1uF / 0603 / 10% / 50V / X5R | CAP CER 1UF 50V X5R 0603 | C2 | TDK | C1608X5R1H105K080AB | Digi-Key | 445-7468-6-ND | 1
10uF / 0805 / 20% / 16V / X7R | CAP CER 10UF 16V X7R 0805 | C3 | Taiyo Yuden | EMK212BB7106MG-T | Mouser | 963-EMK212BB7106MG-T | 1
1uF / 0402 / 10% / 35V / X5R | CAP CER 1UF 35V X5R 0402 | C4 | TDK | C1005X5R1V105K050BC | Newark | 25AC8373 | 1
1.5SMBJ30A | TVS Diode Single Uni-Dir 30V 1.5KW 2-Pin SMB T/R | D1 | Bourns | 1.5SMBJ30A | Arrow Electronics | 1.5SMBJ30A | 1
RB521S30T1G | Rectifier Diode, Schottky, 1 Phase, 1 Element, 0.2A, 30V V(RRM), Silicon | D3 | ON Semiconductor | RB521S30T1G | RSComponents | 7916325P | 1
SF-0603S040-2 | Electric Fuse, Slow Blow, 0.4A, 35VAC, 50VDC, 50A (IR), Surface Mount, 0603 | F1 | Bourns | SF-0603S040-2 | Digi-Key | SF-0603S040-2CT-ND | 1
C2Q300 | Electric Fuse, Very Fast Blow, 0.3A, 32VAC, 63VDC, 35A (IR), Surface Mount, 0603 | F2 | Bel | C2Q300 | Mouser | 530-C2Q300 | 1
2012670005 | USB Connector, 24 Contact(s), Female, Right Angle, Surface Mount Terminal, Locking, Receptacle | J1 | Molex | 2012670005 | Mouser | 538-201267-0005 | 1
SM04B-GHS-TB | 4 Positions Header Connector 1.25mm SMD Right Angle | J2 | JST | SM04B-GHS-TB(LF)(SN) | Future Electronics | 6018129 | 1
SM06B-GHS-TB | JST GH Series Connector, Pitch 1.25 mm, 1 x 6 Position, Right Angle, Height 4.35 mm, -25 to 85 degC, RoHS, Tape and Reel | J3 | JST | SM06B-GHS-TB(LF)(SN) | RSComponents | 7521800 | 1
0436500205 | CONN MALE HEADER R/A 2POS 3MM | J4 | Molex | 0436500205 | Newark | 01AH1232 | 1
ERM8-020-02.0-L-DV-P-TR | Board Stacking Connector, 40 Contact(s), 2 Row(s), Male, Straight, 0.8mm Pitch, Surface Mount Terminal, Black Insulator | J5 | Samtec | ERM8-020-02.0-S-DV-P-TR | Mouser | 200-ERM8-2002SDVPTR | 1
BM02B-GHS-TBT | Disconnectable Crimp Style Connector, Pitch 1.25 mm, 1 x 2 Position, Height 4.05 mm, -25 to 85 degC, RoHS, Tape and Reel | J6 | JST | BM02B-GHS-TBT(LF)(SN) | Future Electronics | 2035020 | 1
DMP4047LFDE-7 | MOSFET P-CH 40V 3.3A 6UDFN | Q1 | Diodes | DMP4047LFDE-7 | Newark | 82Y6592 | 1
5.1K / 0402 / 1% / 0.063W / 100PPM/K | Fixed Resistor, Metal Glaze/thick Film, 0.0625W, 5100ohm, 50V, 5% +/-Tol, 100ppm/Cel, Surface Mount, 0402 | R1 | Yageo | RC0402JR-075K1L | Newark | 68R0016 | 1
7.5K / 0402 / 1% / 0.063W / 100PPM/K | RES 7.5K OHM 1% 1/16W 0402 | R2 | Yageo | RC0402FR-077K5L | Newark | 67R9955 | 1
23.7K / 0402 / 1% / 0.063W / 100PPM/K | RES 23.7K OHM 1% 1/16W 0402 | R3 | Yageo | RC0402FR-0723K7L | Mouser | 603-RC0402FR-0723K7L | 1
47K / 0402 / 1% / 0.063W / 100PPM/K | Fixed Resistor, Metal Glaze/thick Film, 0.0625W, 47000ohm, 50V, 1% +/-Tol, 100ppm/Cel, Surface Mount, 0402 | R4 | Yageo | RC0402FR-0747KL | Digi-Key | 311-47.0KLRDKR-ND | 1
1.8M / 0402 / 1% / 0.063W / 100PPM/K | RES SMD 1.8M OHM 1% 1/16W 0402 | R5 | Samsung | RC1005F185CS | Digi-Key | 1276-4292-1-ND | 1
1.2M / 0402 / 1% / 0.063W / 100PPM/K | Fixed Resistor, Metal Glaze/thick Film, 0.0625W, 1200000ohm, 50V, 1% +/-Tol, 100ppm/Cel, Surface Mount, 0402 | R6 | Yageo | RC0402FR-071M2L | Mouser | 603-RC0402FR-071M2L | 1
17.4K / 0402 / 1% / 0.063W / 100PPM/K | RES SMD 17.4K OHM 1% 1/16W 0402 | R7 | Vishay Dale | CRCW040217K4FKEDC | Arrow Electronics | CRCW040217K4FKEDC | 1
LTM8074EY#PBF | Switching Regulator, Current-mode, 2200kHz Switching Freq-Max, PBGA25 | U1 | Analog Devices | LTM8074IY#PBF |  |  | 1

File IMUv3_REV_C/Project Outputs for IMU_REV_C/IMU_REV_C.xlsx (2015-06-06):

Manufacturer 1 | Manufacturer Part Number 1 | Description | Designator | Value | Quantity | Footprint
Yageo | CC0805ZKY5V6BB106 | Capacitor, 10uF, 10V, Y5V, 0805, Ceramic | C1, C4, C6, C13 | 10u | 4 | 0805-CAP
Yageo | CC0402ZRY5V7BB104 | Capacitor, 0.1uF, 16V, Y5V, 0402, Ceramic | C2, C5, C10, C12, C14 | 0u1 | 5 | 0402-CAP
Yageo | CC0402KRX7R7BB103 | Capacitor, 10000pF, 16V, 10%, X7R, 0402, Ceramic | C3 | 10000pF | 1 | 0402-CAP
TDK Corporation | C1005X5R1C474K050BC | Capacitor, 0.47uF, 16V, 10%, X5R, 0402, Ceramic | C7 | 0u47 | 1 | 0402-CAP
TDK Corporation | C1608X6S1C225K080AC | Capacitor, 2.2uF, 16V, 10%, X6S, 0603, Ceramic | C8, C9 | 2u2 | 2 | 0603-CAP
AVX Corporation | 06033C103JAT2A | Capacitor, 10000pF, 25V, 5%, X7R, 0603, Ceramic | C11 | 10000pF | 1 | 0603-CAP
PennEngineering | PEM-SMTSO-M1.6-2-ET | Fastener, M1.6x2mm, SMTSO, Carbon Steel | Nut 1, Nut 2, Nut 3, Nut 4 |  | 4 | PEM-SMTSO-M1.6-2-ET
Hirose Electric Co Ltd | DF40C-20DP-0.4V(51) | Connector, HDR, 20Pos, 0.4mm, SMD, GOLD | P1 | DF40C-20DP-0.4V(51) | 1 | DF40C-20-DP
STMICROELECTRONICS | L3GD20 | Sensor, Low-power, Three-axis, Angular rate | U1 |  | 1 | L3GD20
STMicroelectronics | LSM303DTR | Module, 3D Accelerometer, 3D Magnetometer | U2 |  | 1 | LSM303D
InvenSense | MPU-6000 | 3 Axis Accel, 3Axis Gyro | U3 |  | 1 | QFN-24
Measurement Specialties, Inc. | MS561101BA03-50 | Board, Digital pressure sensor I2C/SPI | U4 |  | 1 | MS5611-01BA

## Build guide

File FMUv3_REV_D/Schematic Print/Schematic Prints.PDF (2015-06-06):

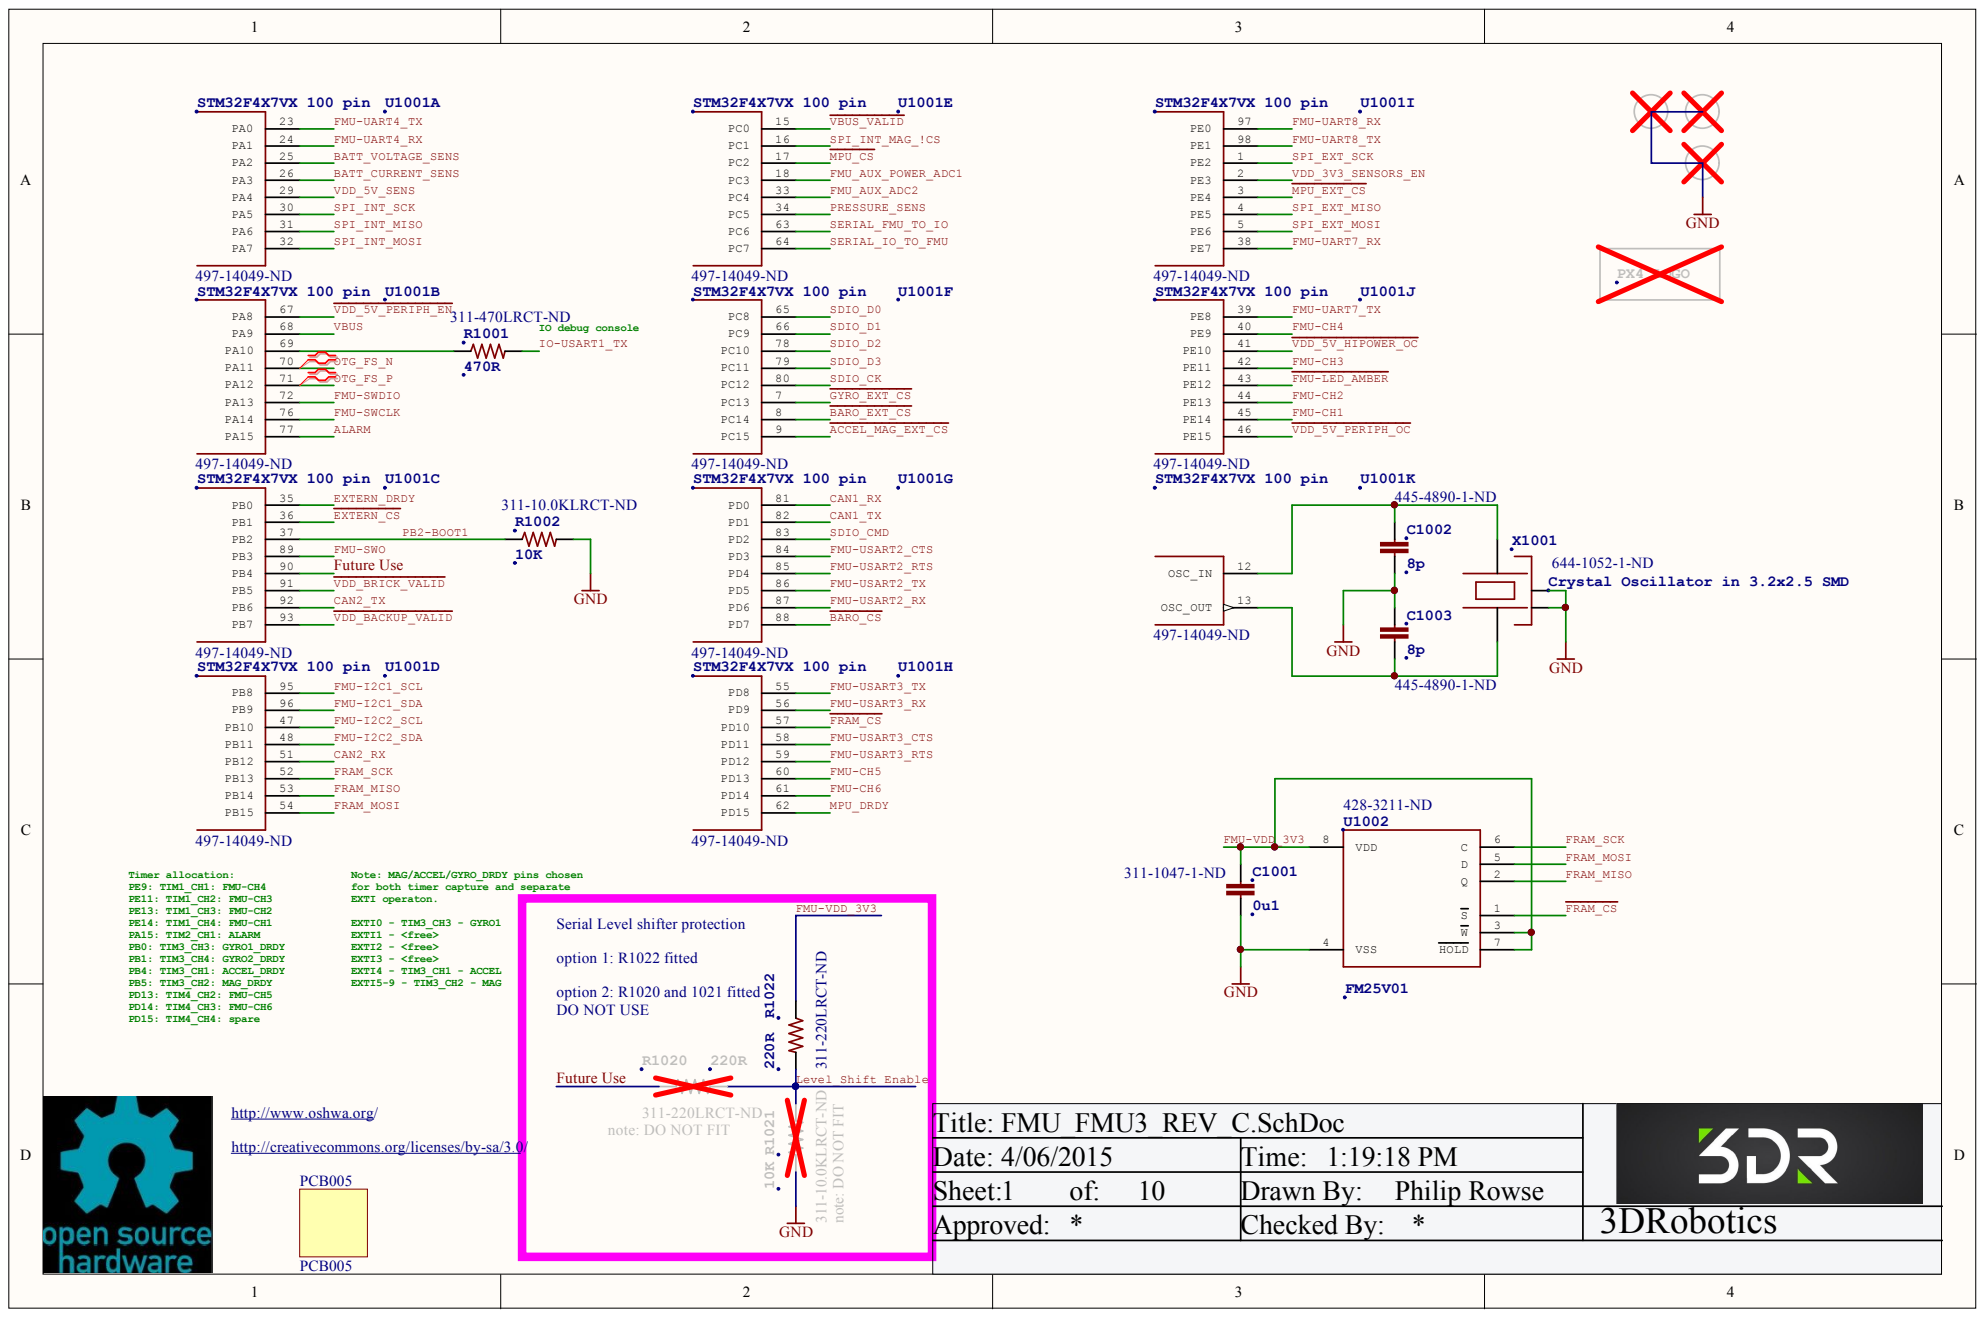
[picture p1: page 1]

Note: MAG/ACCEL/GYRO_DRDY pins chosen
for both timer capture and separate
EXTI operaton.

Serial Level shifter protection

http://www.oshwa.org/

311-220LRCT-ND
note: DO NOT FIT

Title: FMU_FMU3_REV_C.SchDoc
Date: 4/06/2015 | Time: 1:19:18 PM
Sheet:1 of: 10 | Drawn By: Philip Rowse
Approved: * | Checked By: * | 3DRobotics

http://creativecommons.org/licenses/by-sa/3.0/

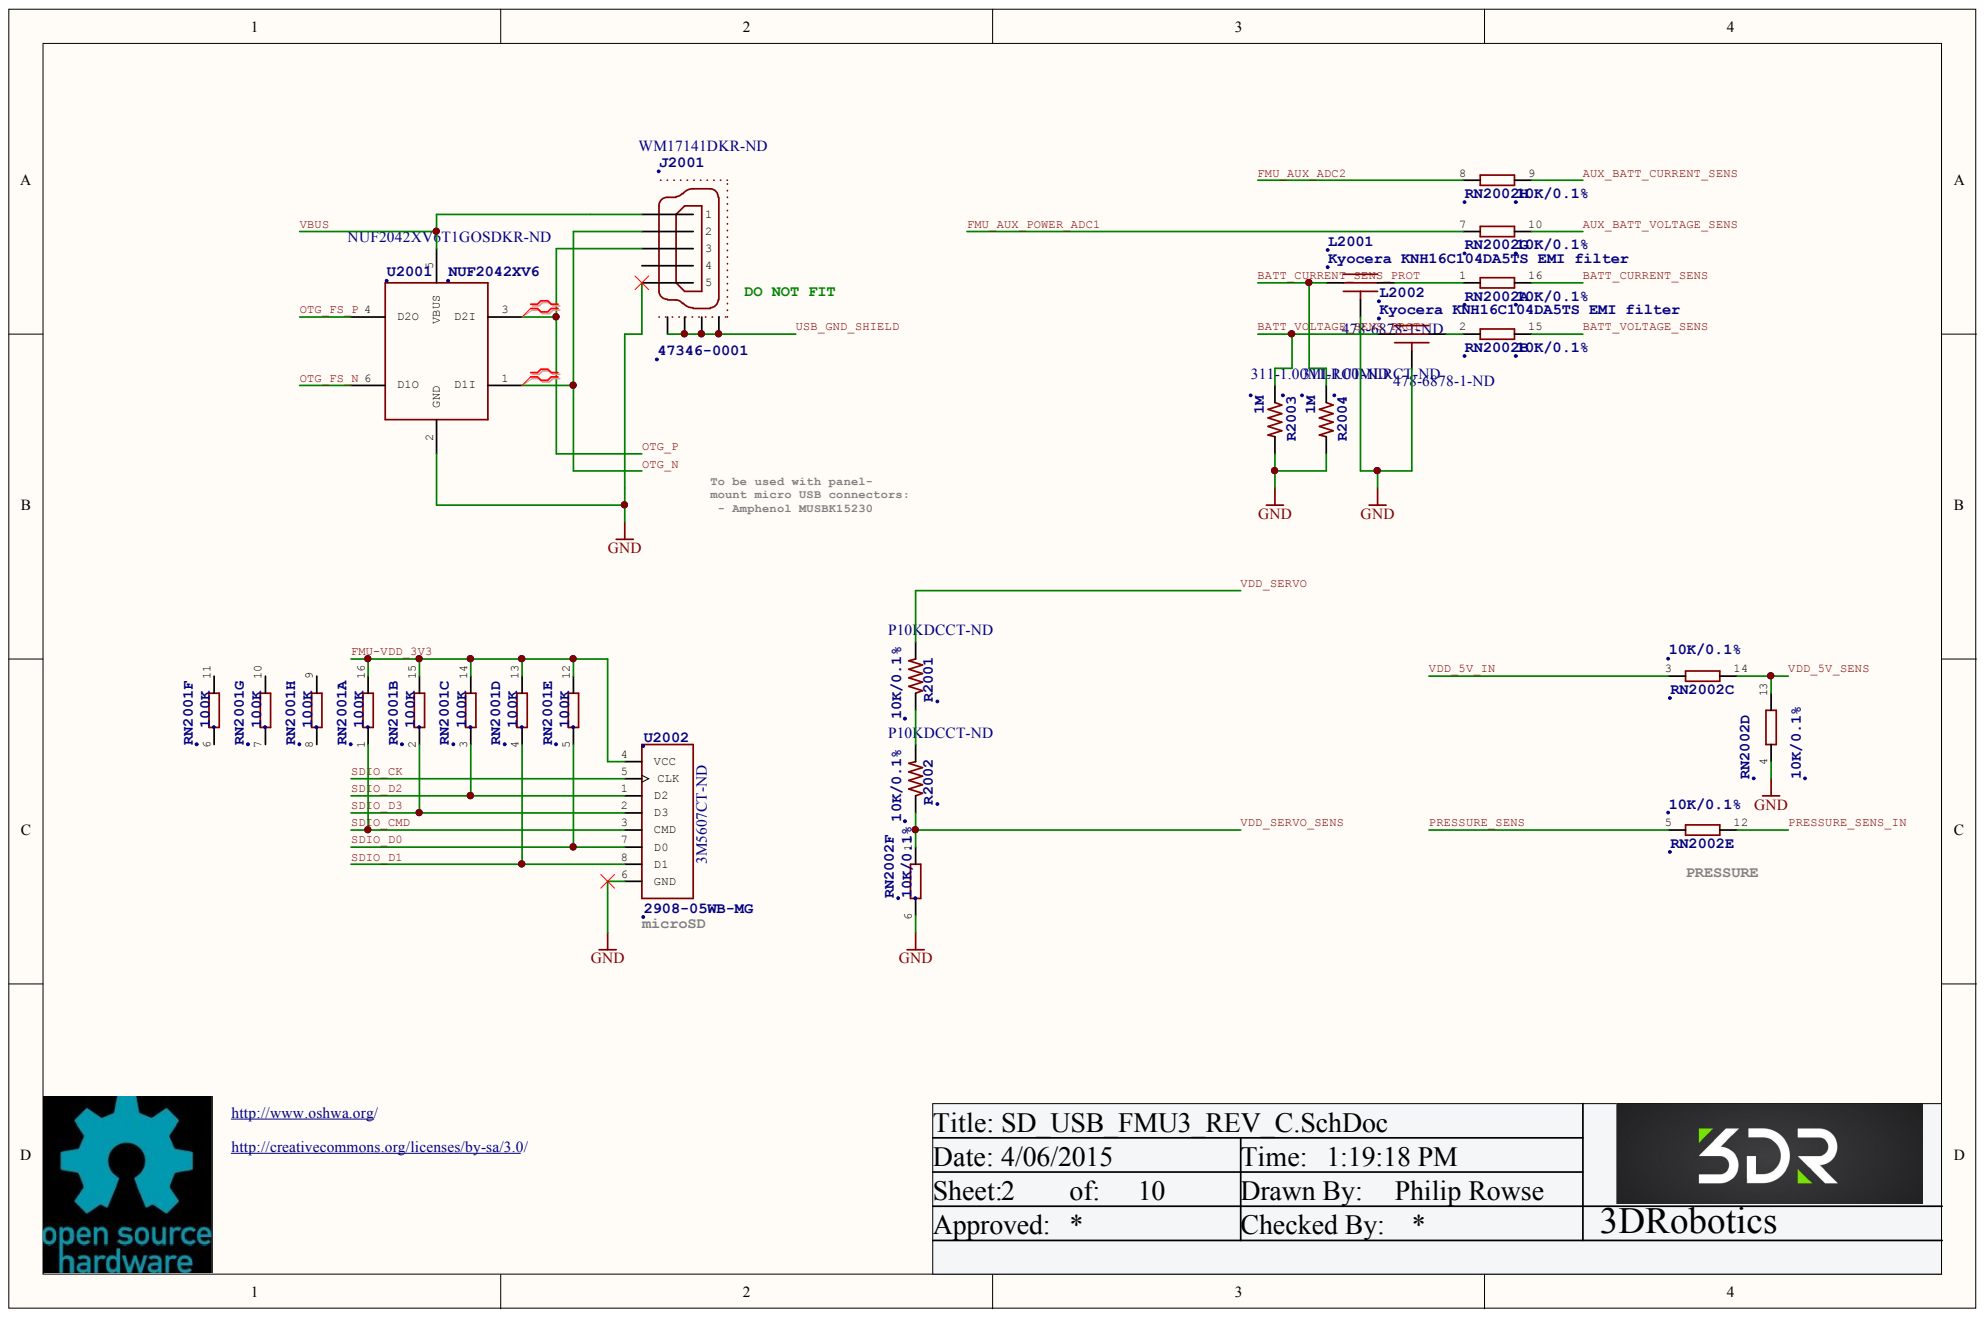
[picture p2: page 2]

Kyocera KNH16C104DA5TS EMI filter 478-6878-1-ND

Title: SD_USB_FMU3 _REV_C.SchDo c
Date: 4/0 6/2 0 1 5 | Time: 1:1 9:1 8 PM
Sheet: 2 of: 1 0 | Drawn By : Philip Rowse
Ap pro ved : * | Checked By : * | 3DRobotics

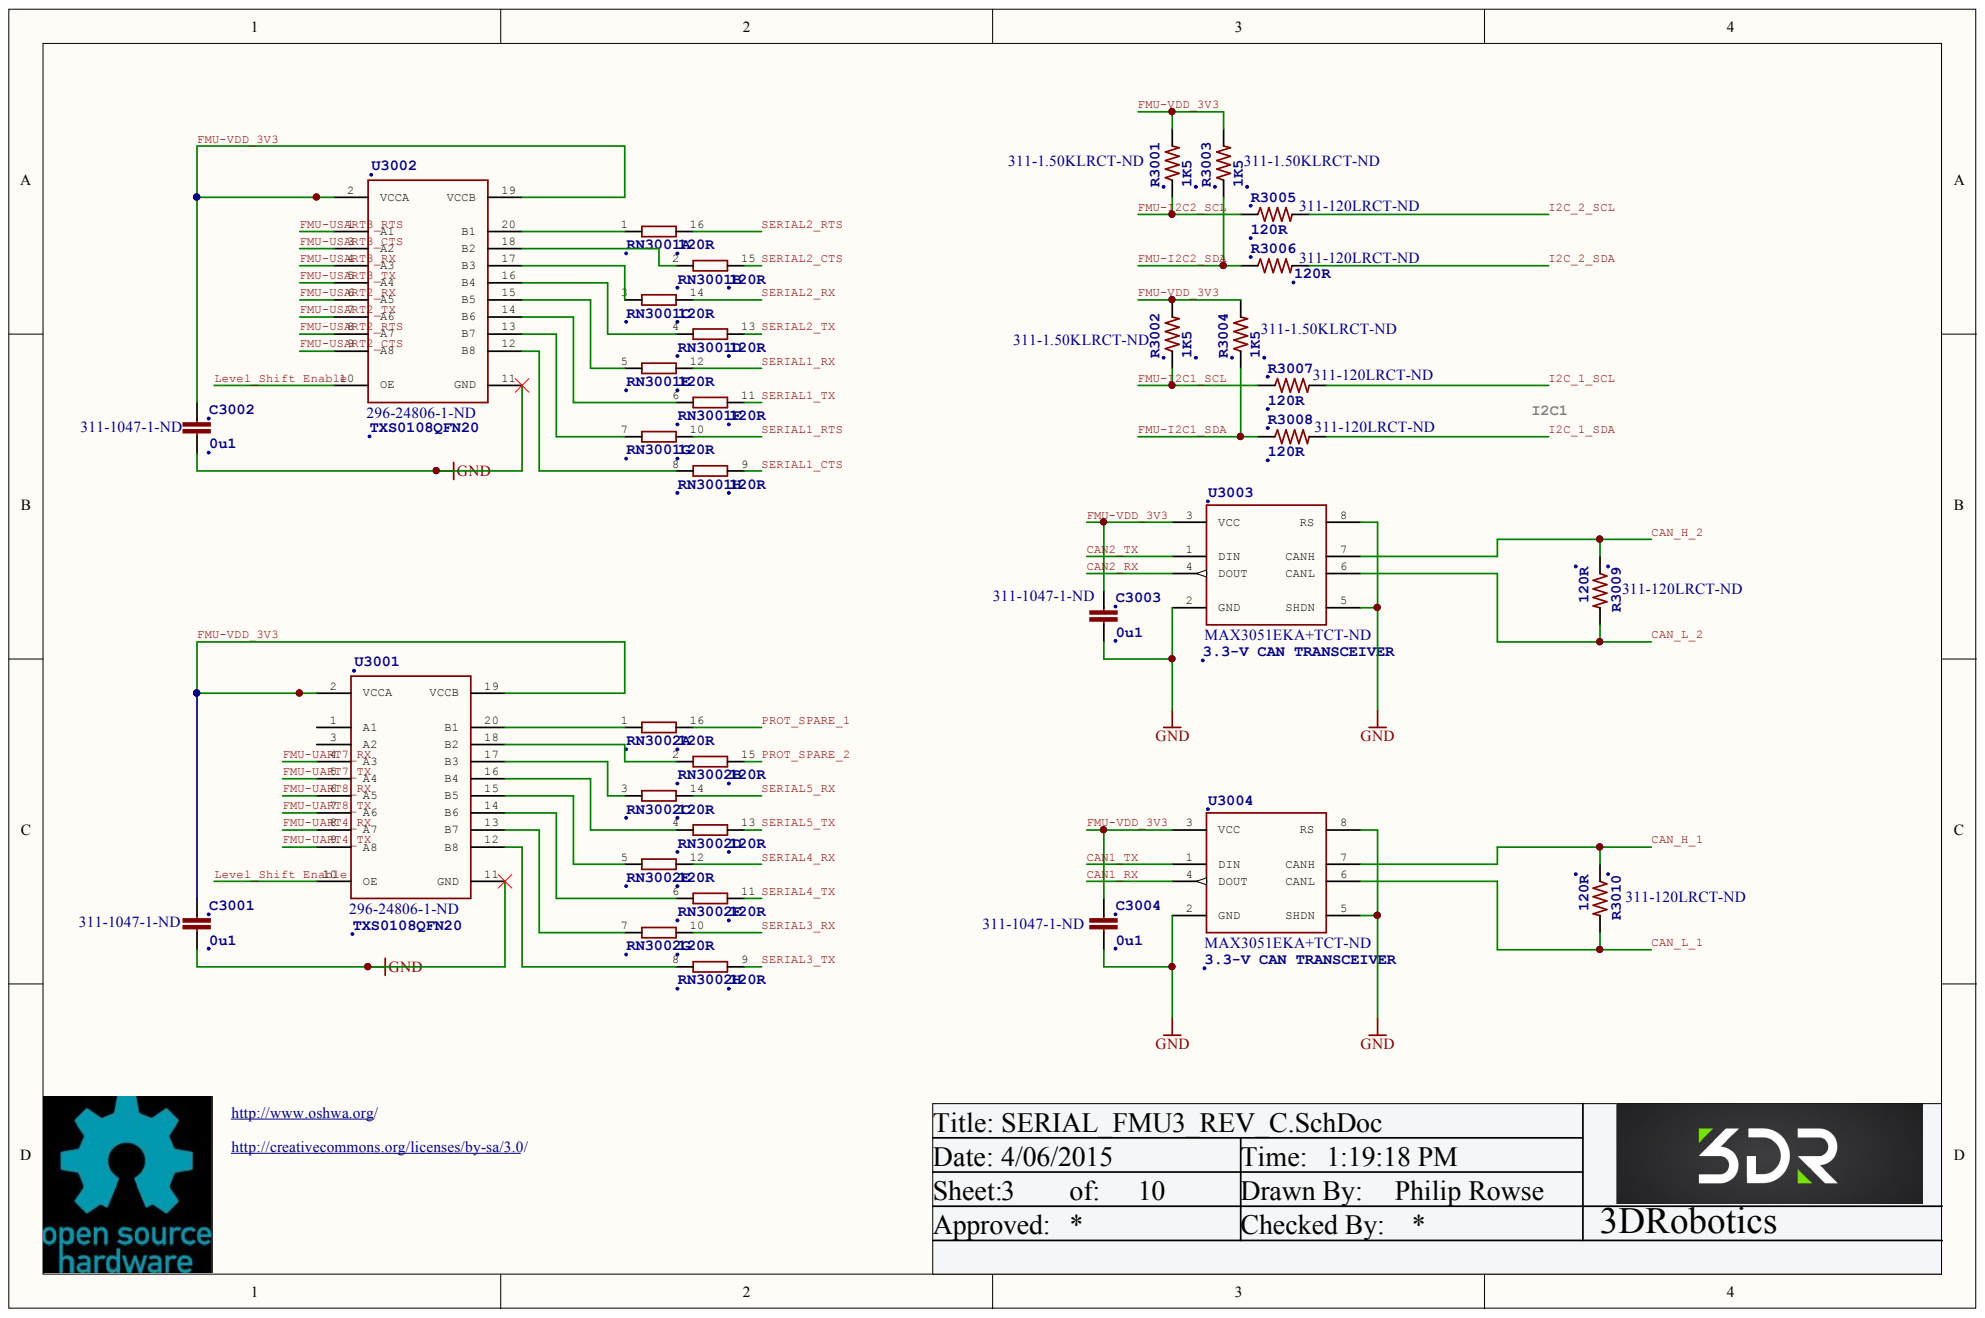
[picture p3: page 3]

Title: SERIAL_FMU3 _REV_C.SchDo c
Date: 4/0 6/2 0 1 5 | Time: 1:1 9:1 8 PM
Sheet: 3 of: 1 0 | Drawn By : Philip Rowse
Ap pro ved : * | Checked By : * | 3DRobotics

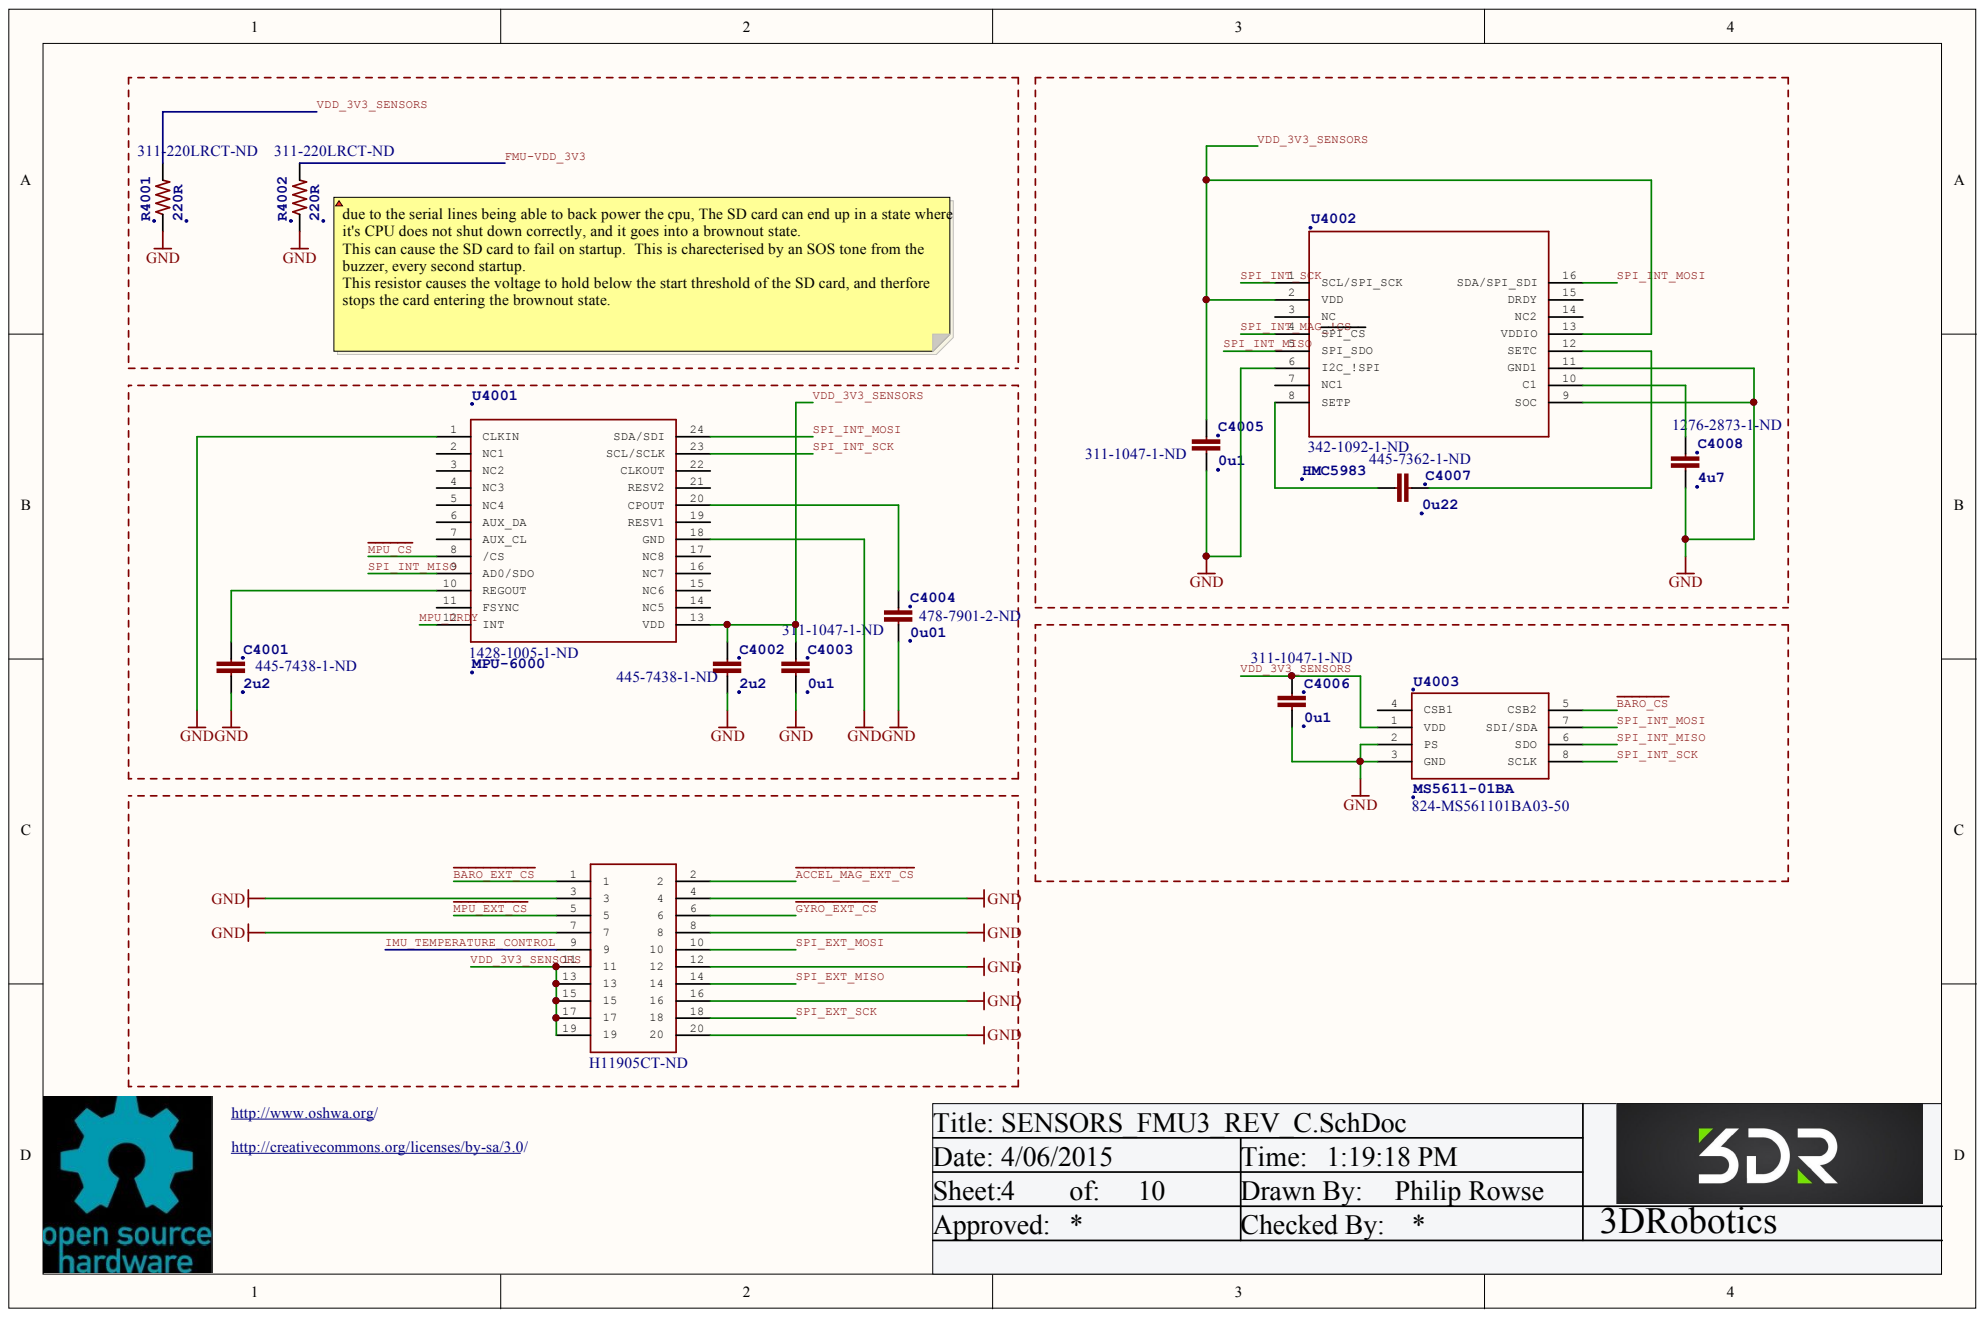
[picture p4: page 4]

he SD card, an

Title: SENSORS_FMU3 _REV_C.SchDo c
Date: 4/0 6/2 0 1 5 | Time: 1:1 9:1 8 PM
Sheet: 4 of: 1 0 | Drawn By : Philip Rowse
Ap pro ved : * | Checked By : * | 3DRobotics

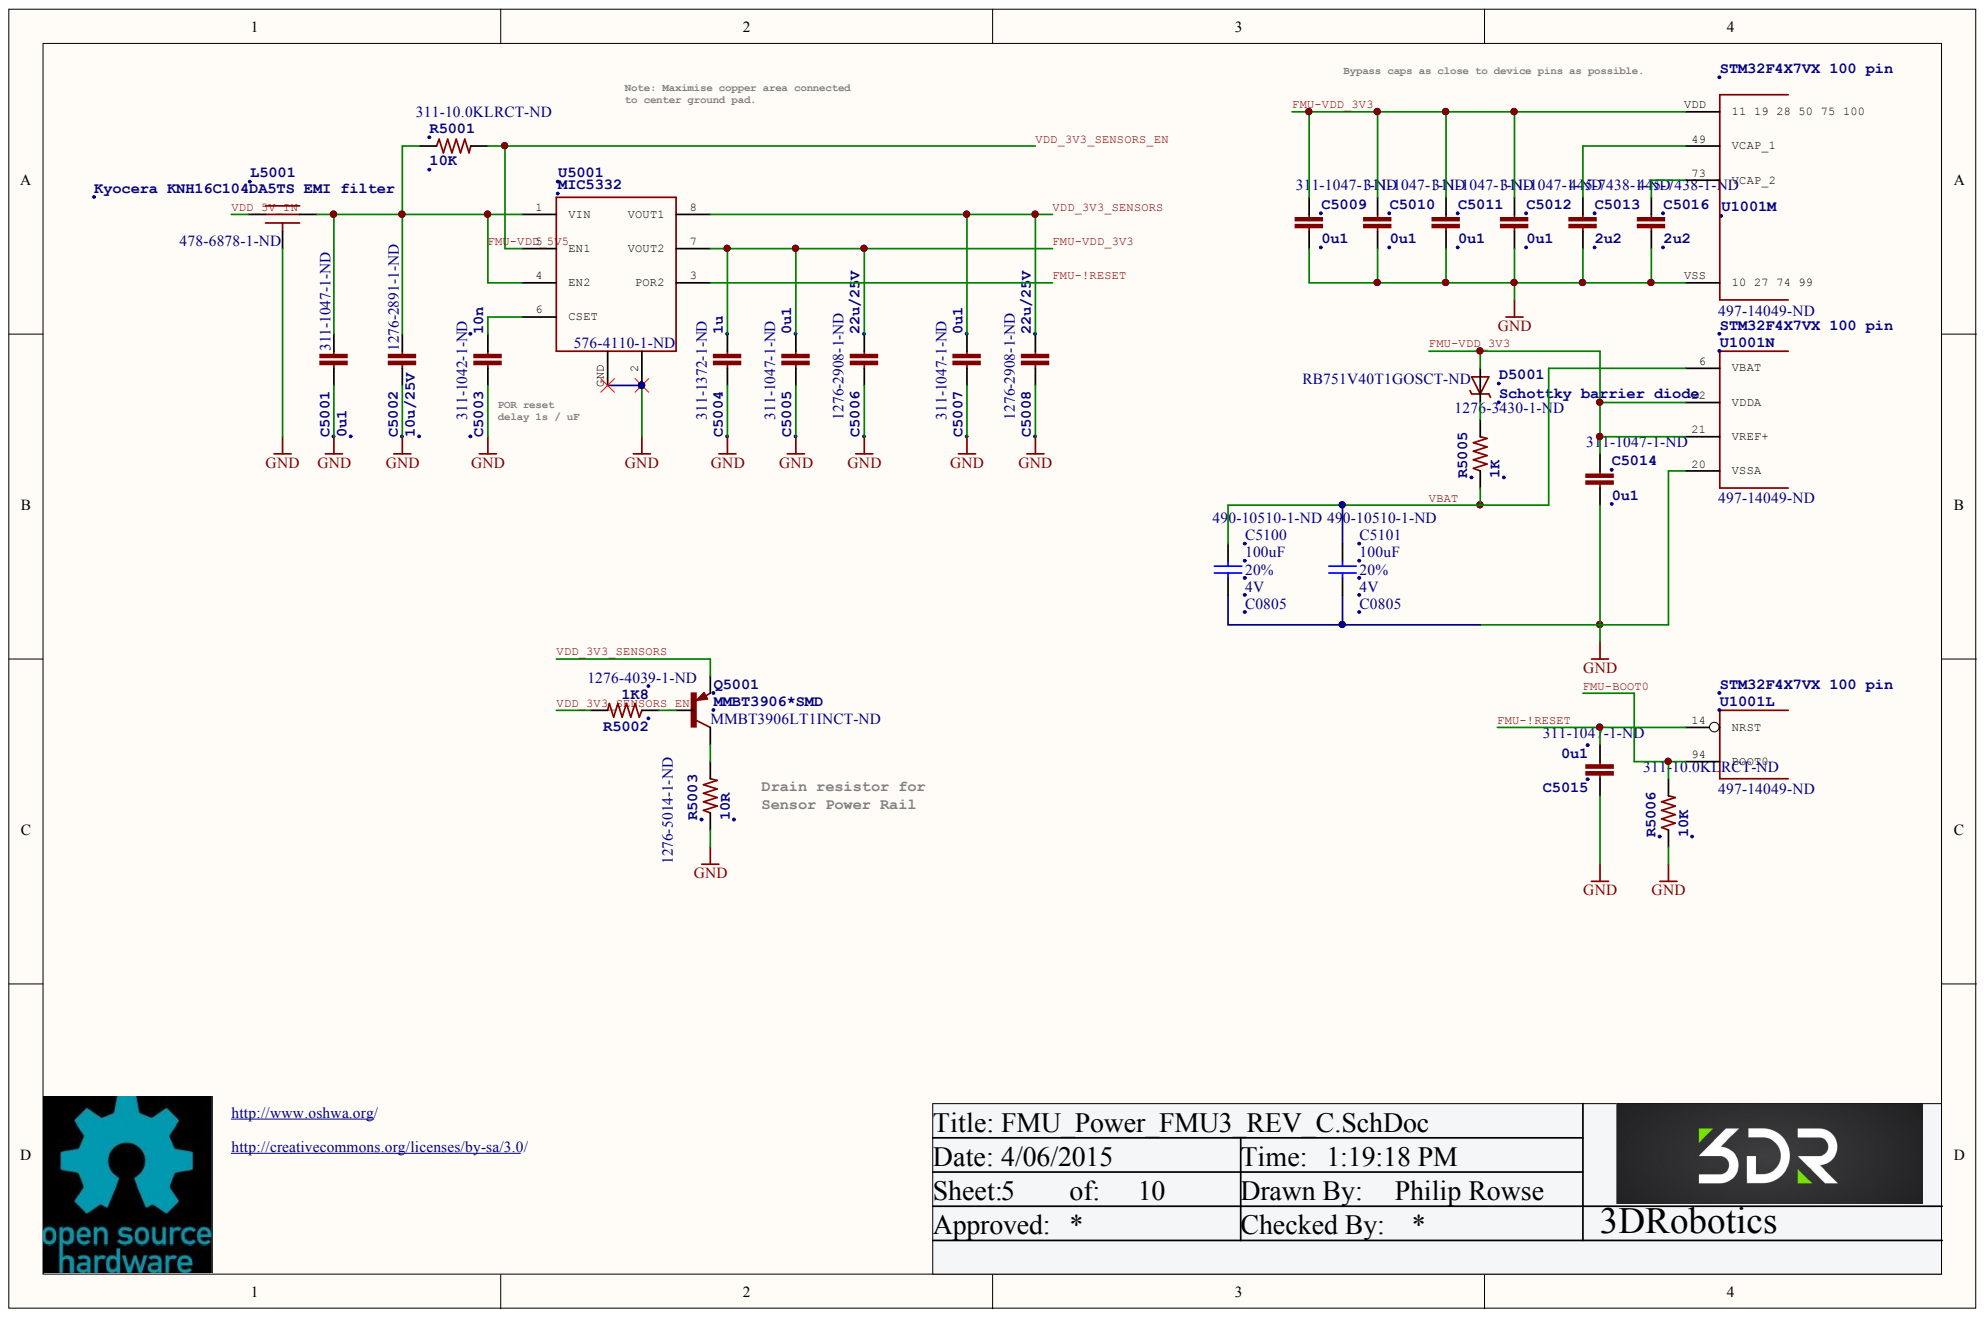
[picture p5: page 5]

Title: FMU_Power_FMU3 _REV_C.SchDo c
Date: 4/0 6/2 0 1 5 | Time: 1:1 9:1 8 PM
Sheet: 5 of: 1 0 | Drawn By : Philip Rowse
Ap pro ved : * | Checked By : * | 3DRobotics

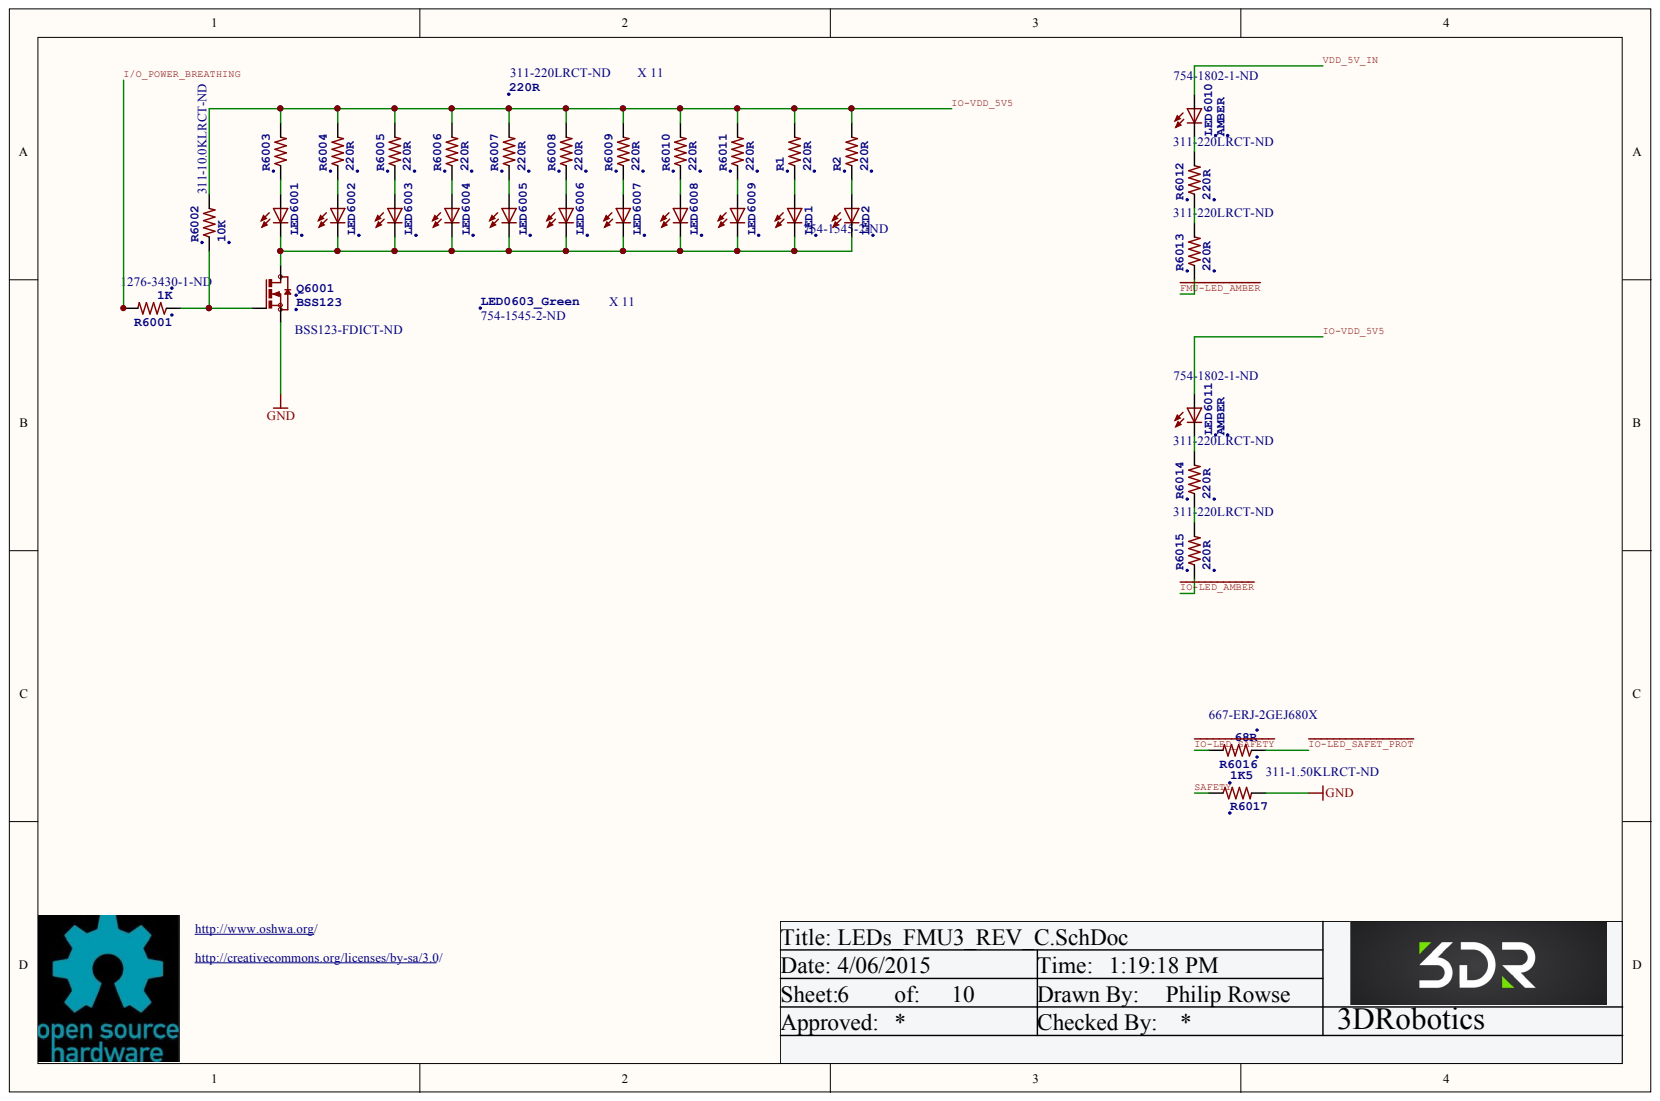
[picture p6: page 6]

Title: LEDs_FMU3 _REV_C.SchDo c
Date: 4/0 6/2 0 1 5 | Time: 1:1 9:1 8 PM
Sheet: 6 of: 1 0 | Drawn By : Philip Rowse
Ap pro ved : * | Checked By : * | 3DRobotics

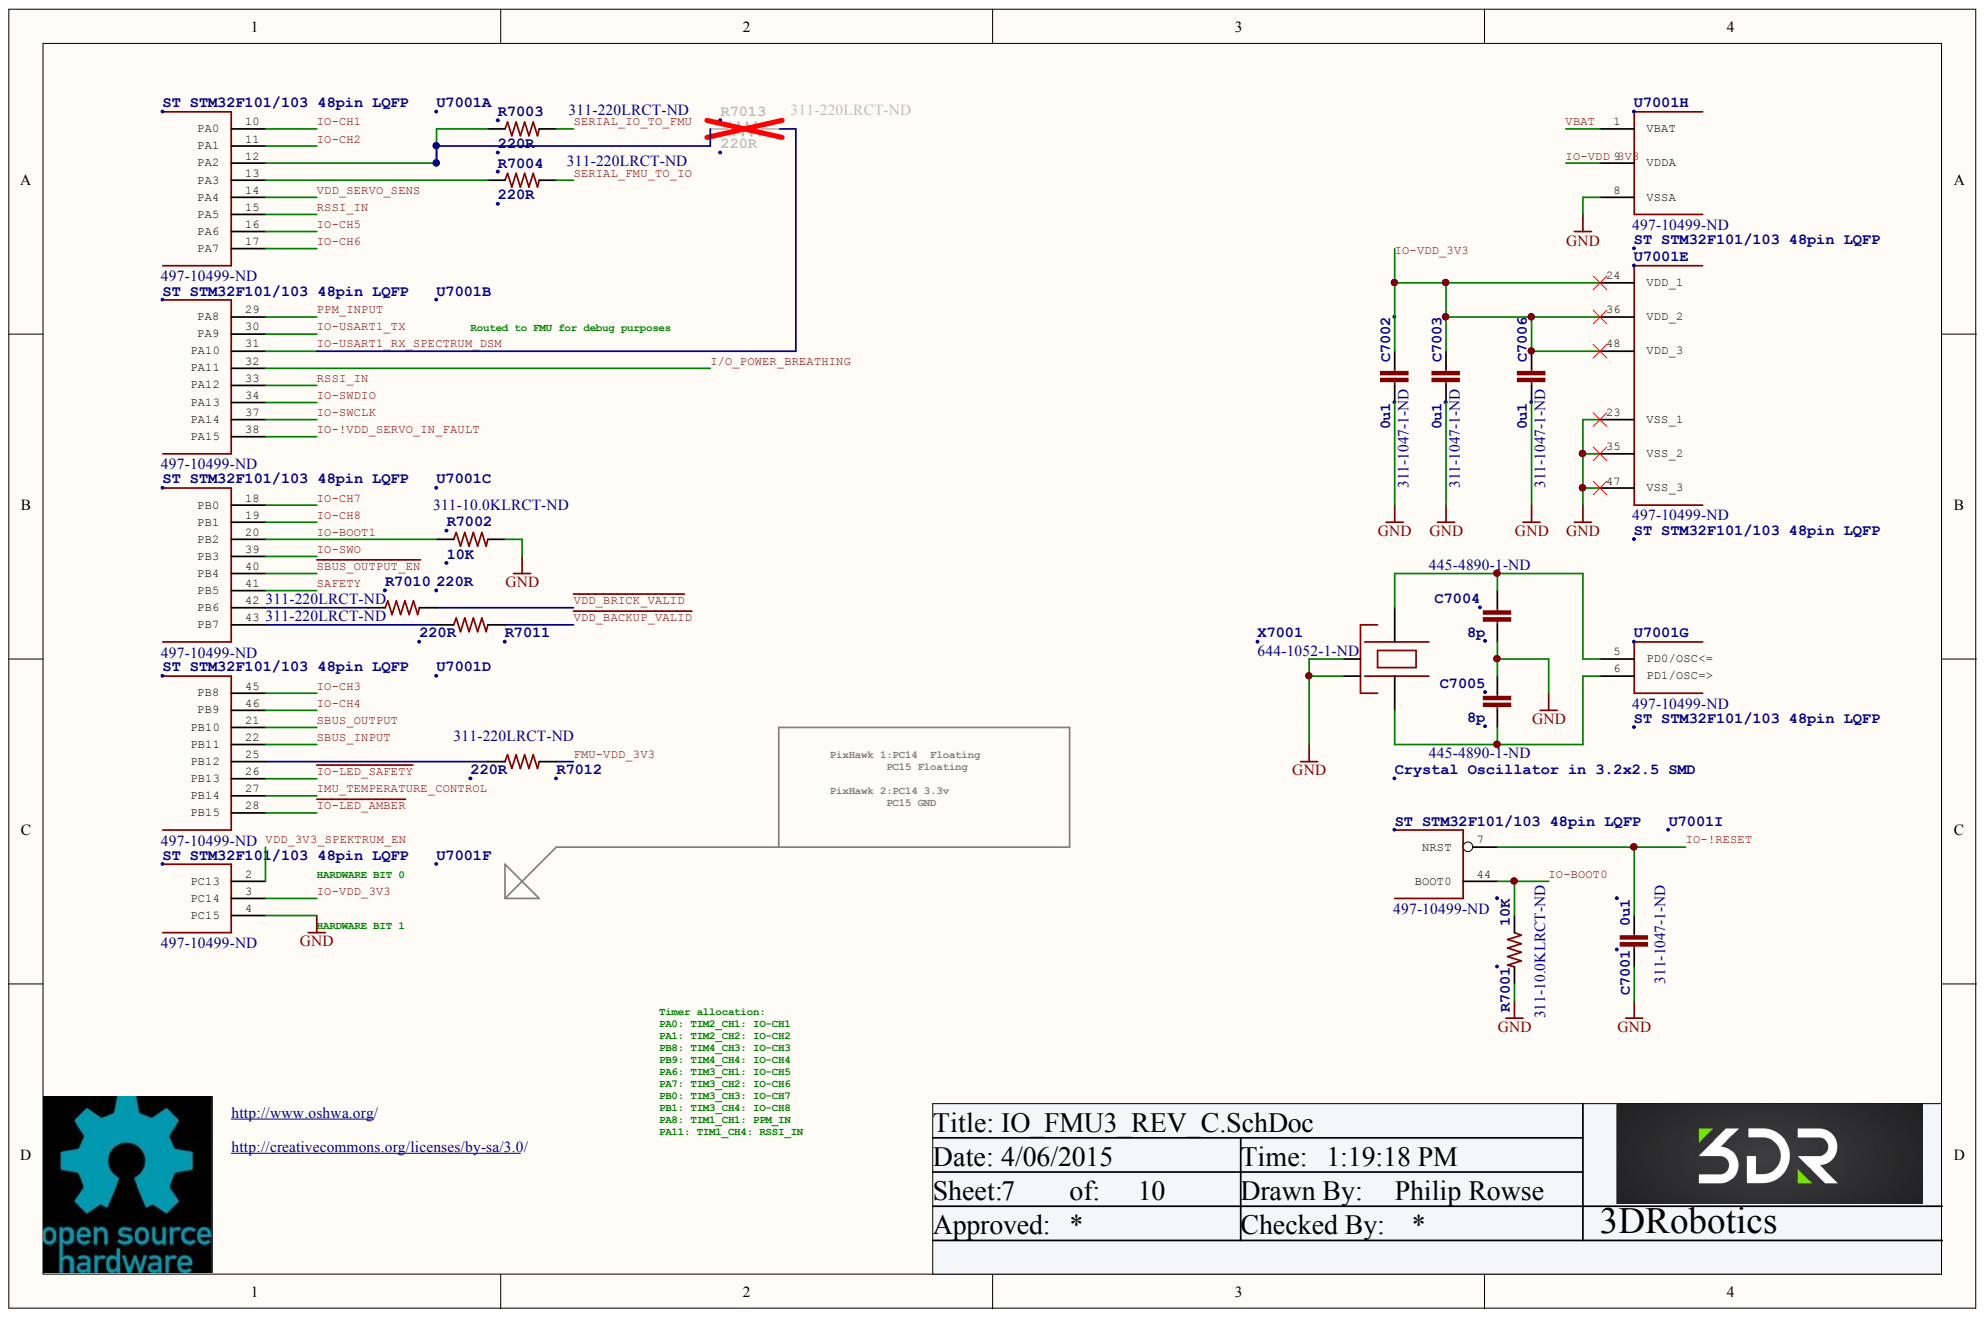
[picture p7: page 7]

1 1 | I O -C H 2 | 220R
1 2

Crystal Oscillator in 3.2x2.5 SMD 311-1047-1-ND C7006 0u1 311-1047-1-ND C7003 0u1 311-1047-1-ND

Title: IO_FMU3 _REV_C.SchDo c
Date: 4/0 6/2 0 1 5 | Time: 1:1 9:1 8 PM
Sheet: 7 of: 1 0 | Drawn By : Philip Rowse
Ap pro ved : * | Checked By : * | 3DRobotics

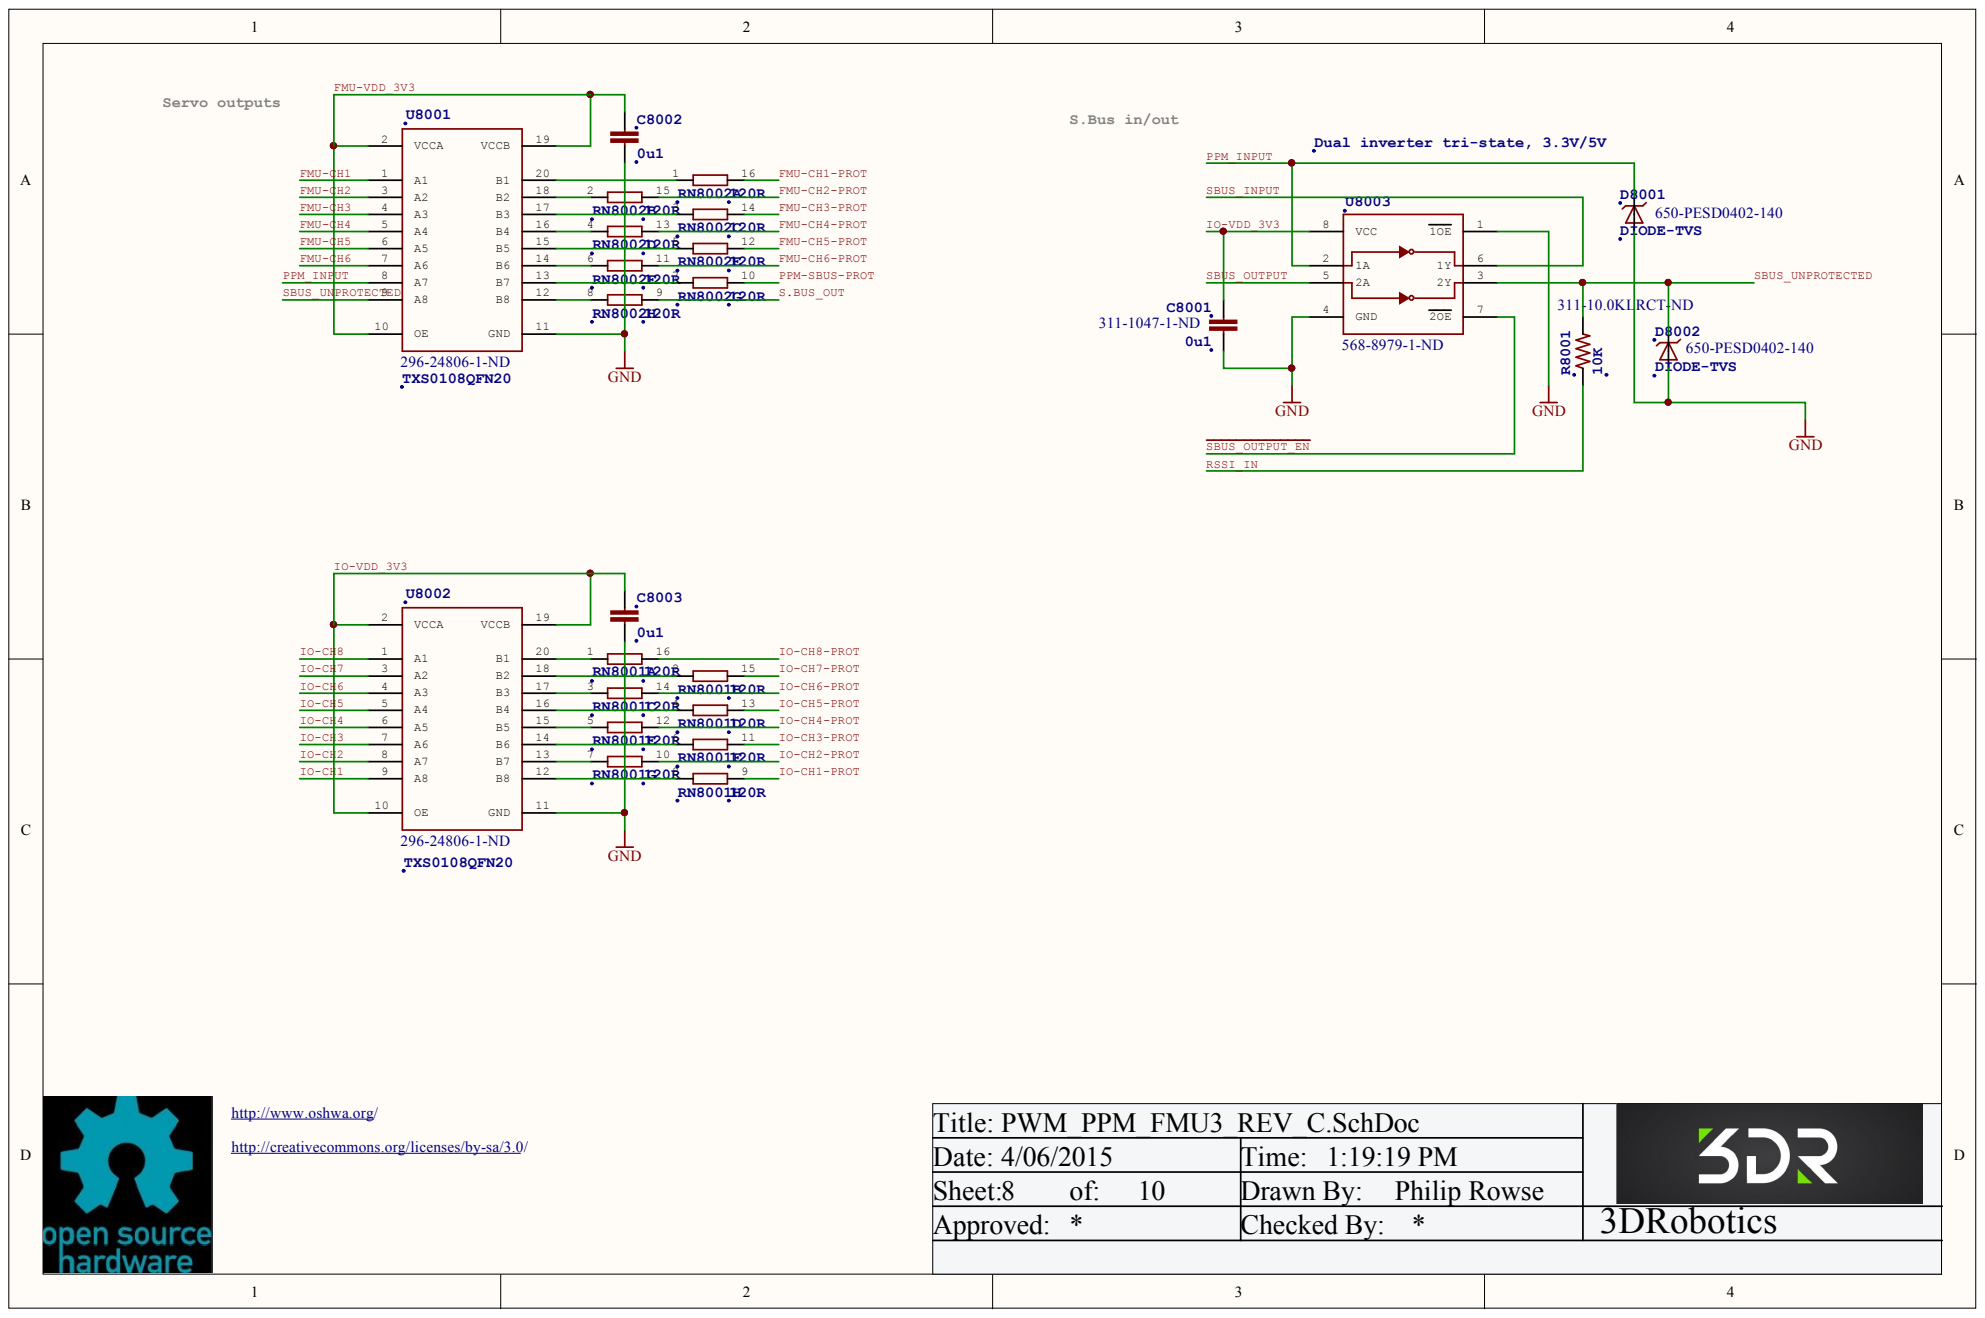
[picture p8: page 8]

Dual inverter tri-state, 3.3V/5V 311-10.0

Title: PWM _PPM _FMU3 _REV_C.SchDo c
Date: 4/0 6/2 0 1 5 | Time: 1:1 9:1 9 PM
Sheet: 8 of: 1 0 | Drawn By : Philip Rowse
Ap pro ved : * | Checked By : * | 3DRobotics

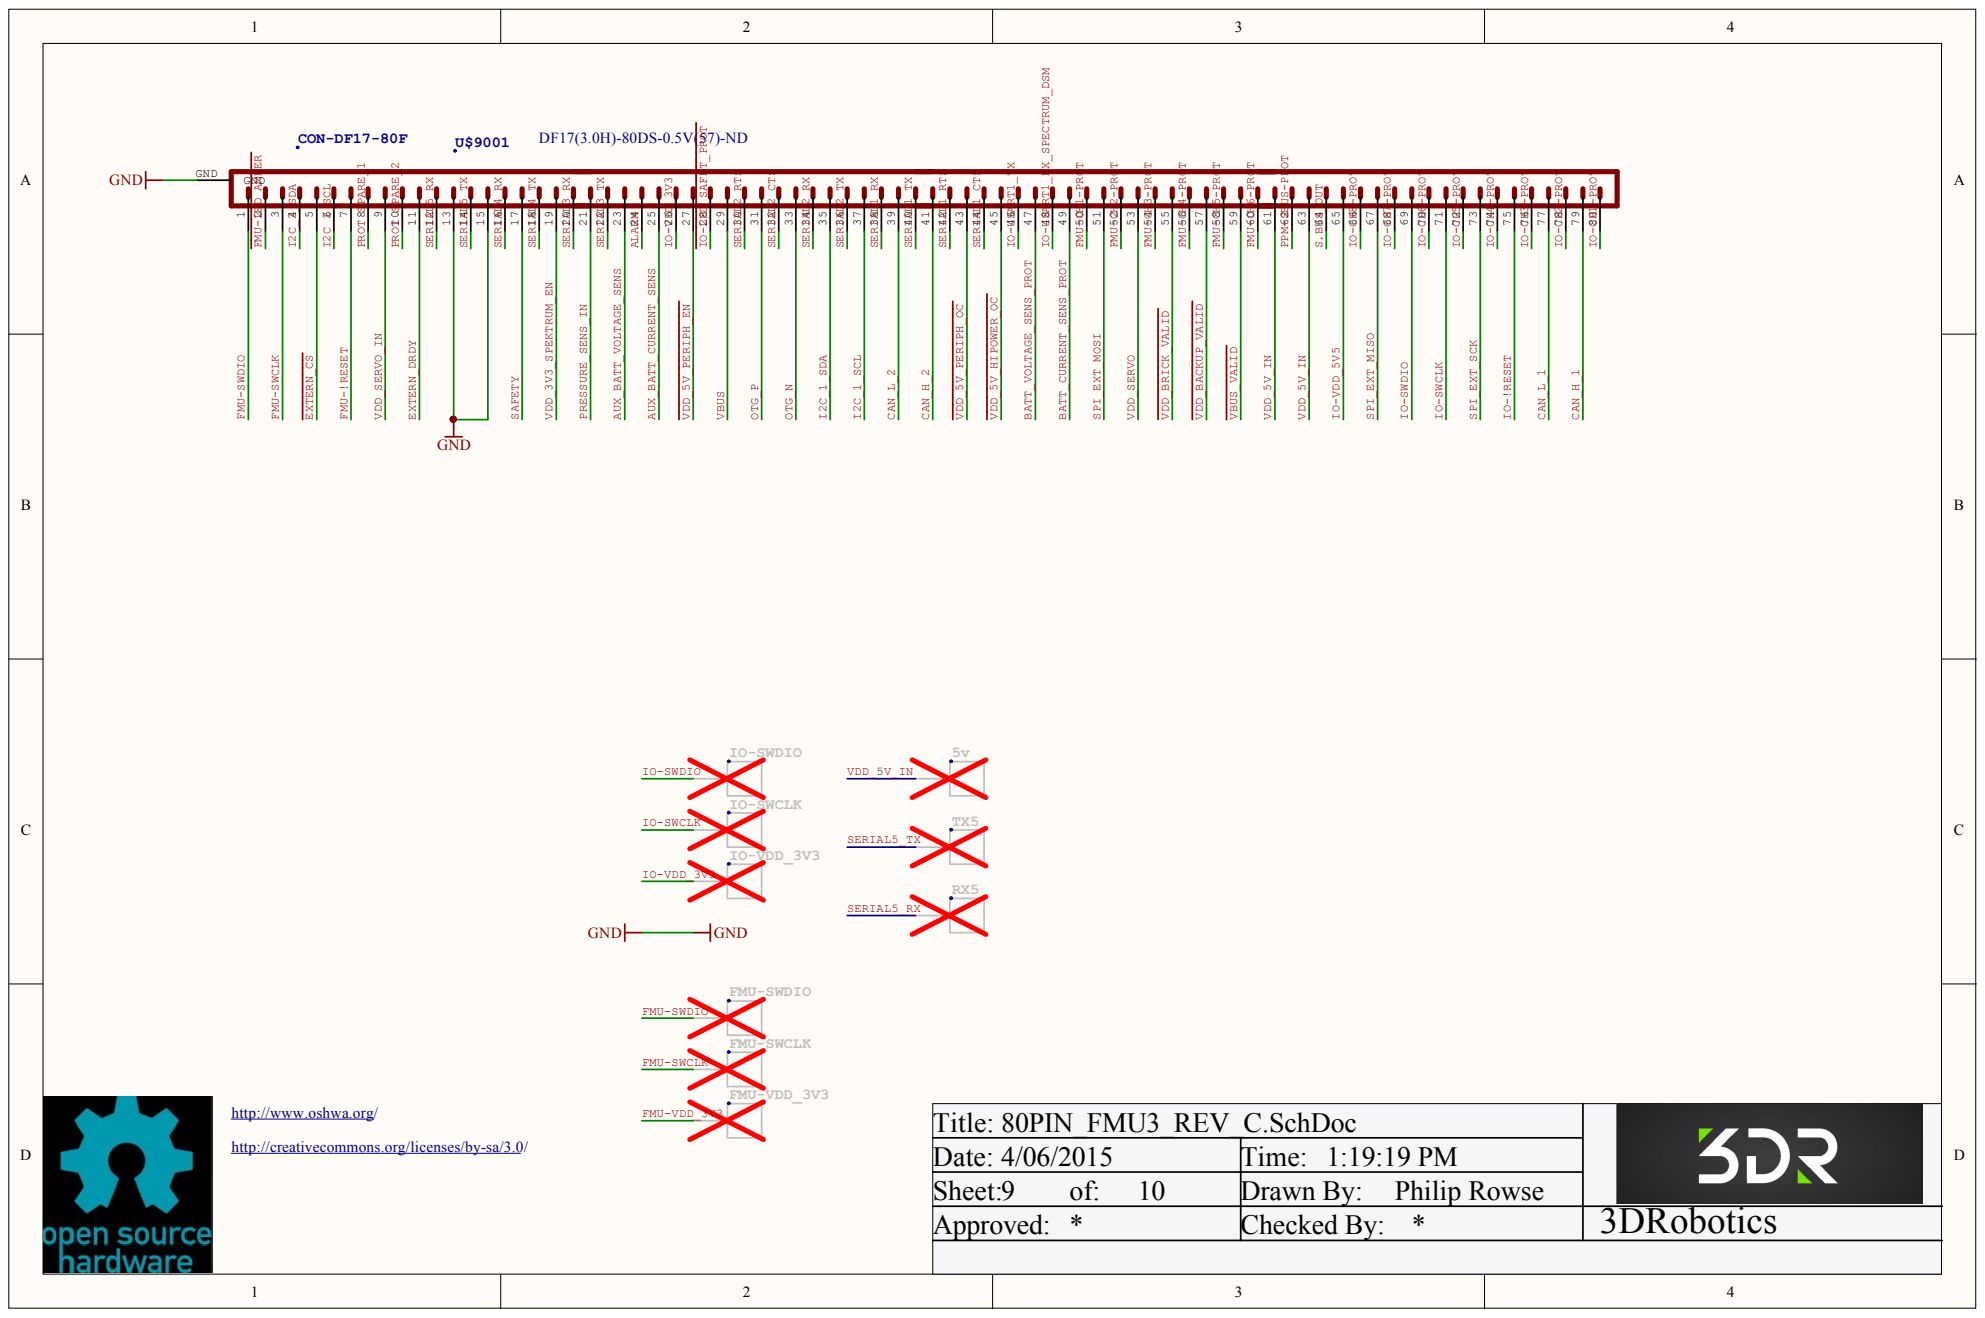
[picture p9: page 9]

http://www.oshwa.org/

Title: 80PIN_FMU3_REV_C.SchDoc
Date: 4/06/2015 | Time: 1:19:19 PM
Sheet:9 of: 10 | Drawn By: Philip Rowse
Approved: * | Checked By: * | 3DRobotics

http://creativecommons.org/licenses/by-sa/3.0/

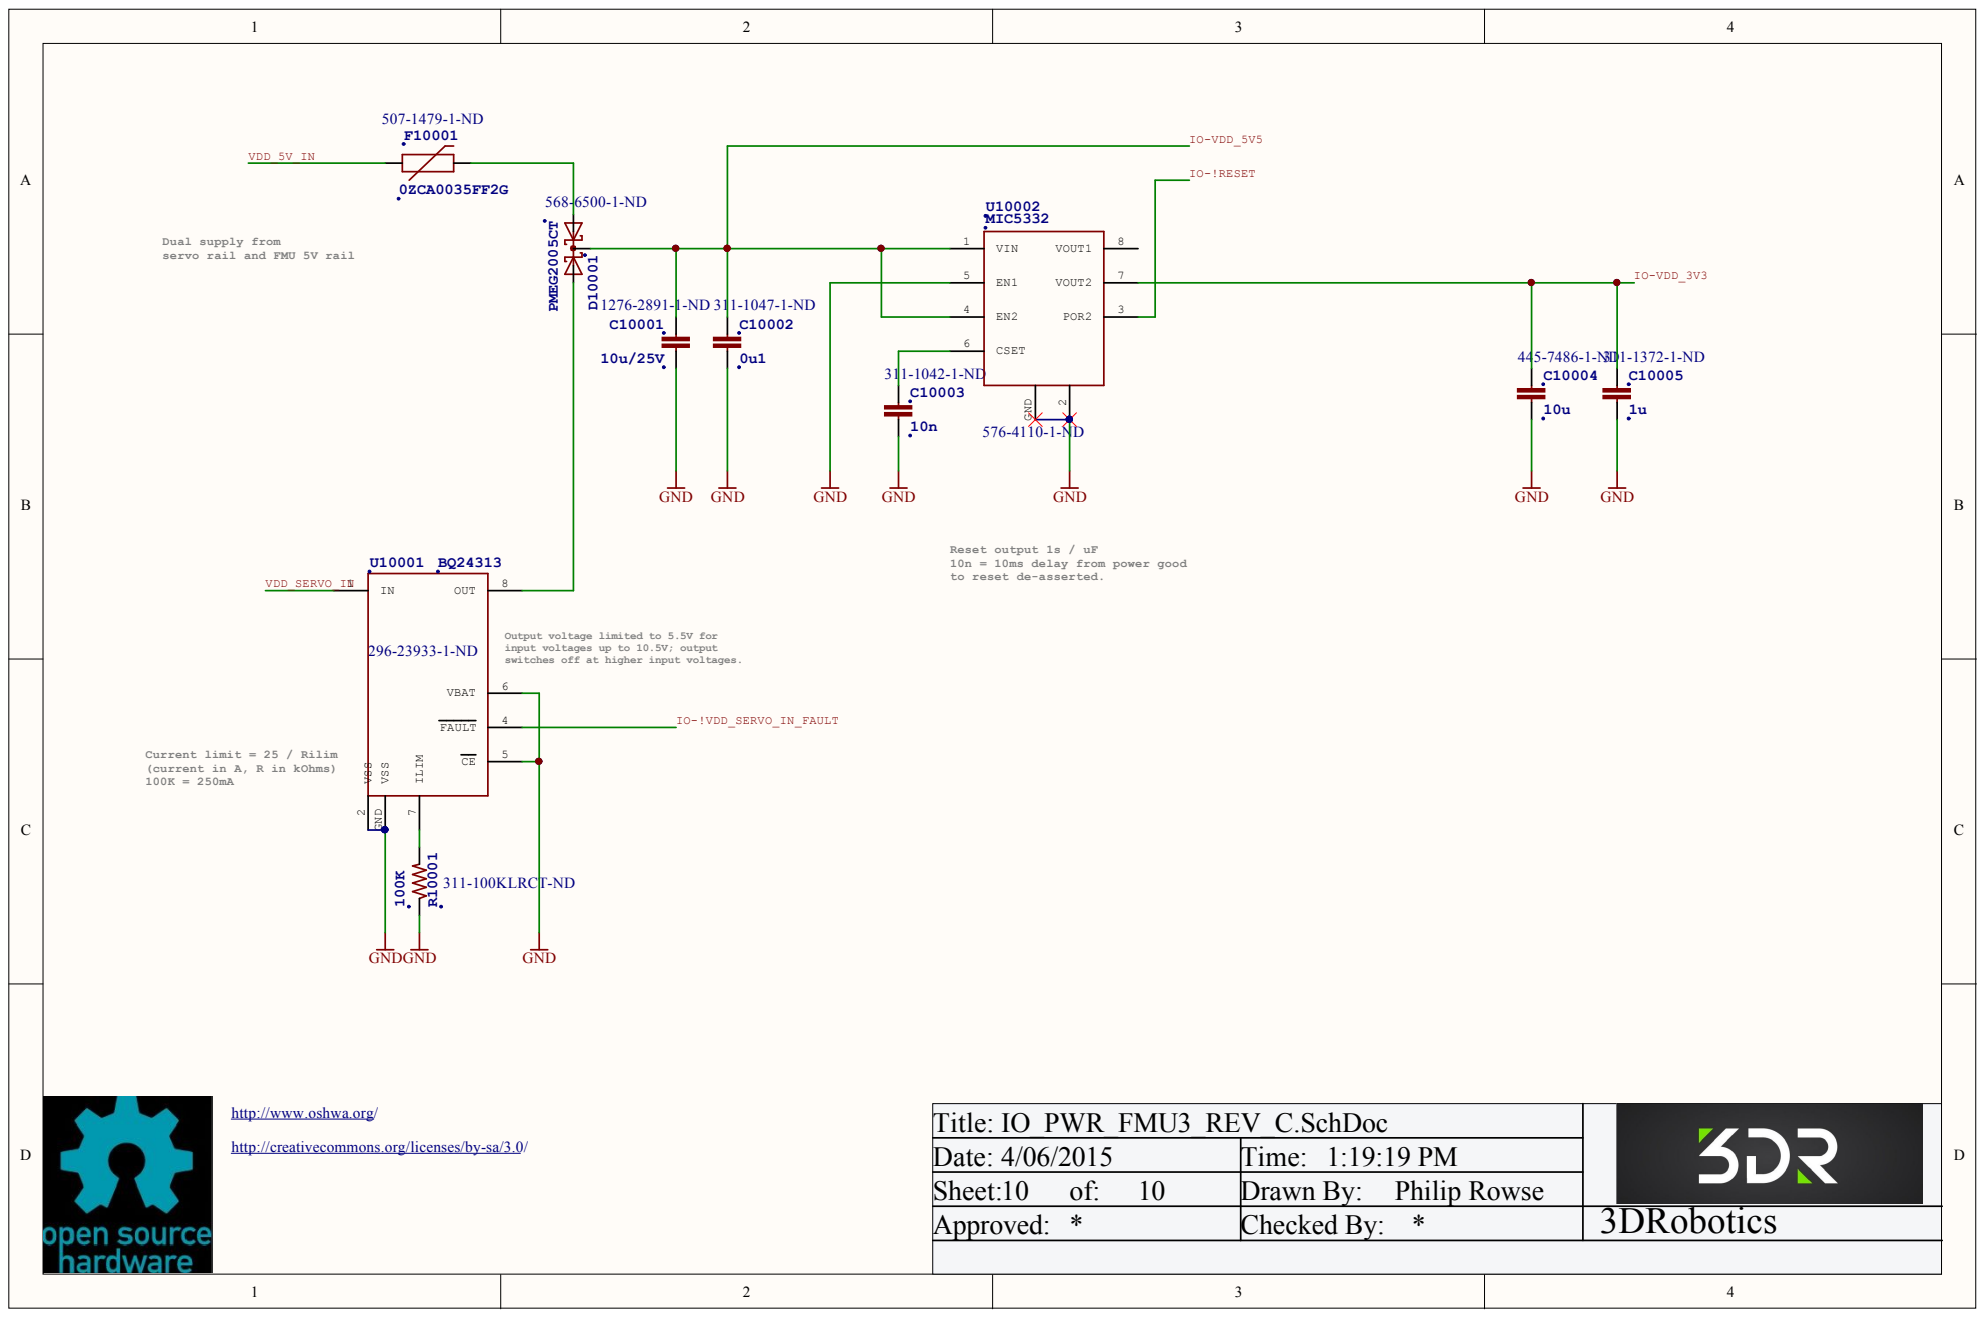
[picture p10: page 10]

Dual supply from
servo rail and FMU 5V rail

Reset output 1s / uF
10n = 10ms delay from power good
to reset de-asserted.

Output voltage limited to 5.5V for
input voltages up to 10.5V; output
switches off at higher input voltages.

Current limit = 25 / Rilim
(current in A, R in kOhms)

http://www.oshwa.org/

Title: IO_PWR_FMU3_REV_C.SchDoc
Date: 4/06/2015 | Time: 1:19:19 PM
Sheet:10 of: 10 | Drawn By: Philip Rowse
Approved: * | Checked By: * | 3DRobotics

http://creativecommons.org/licenses/by-sa/3.0/

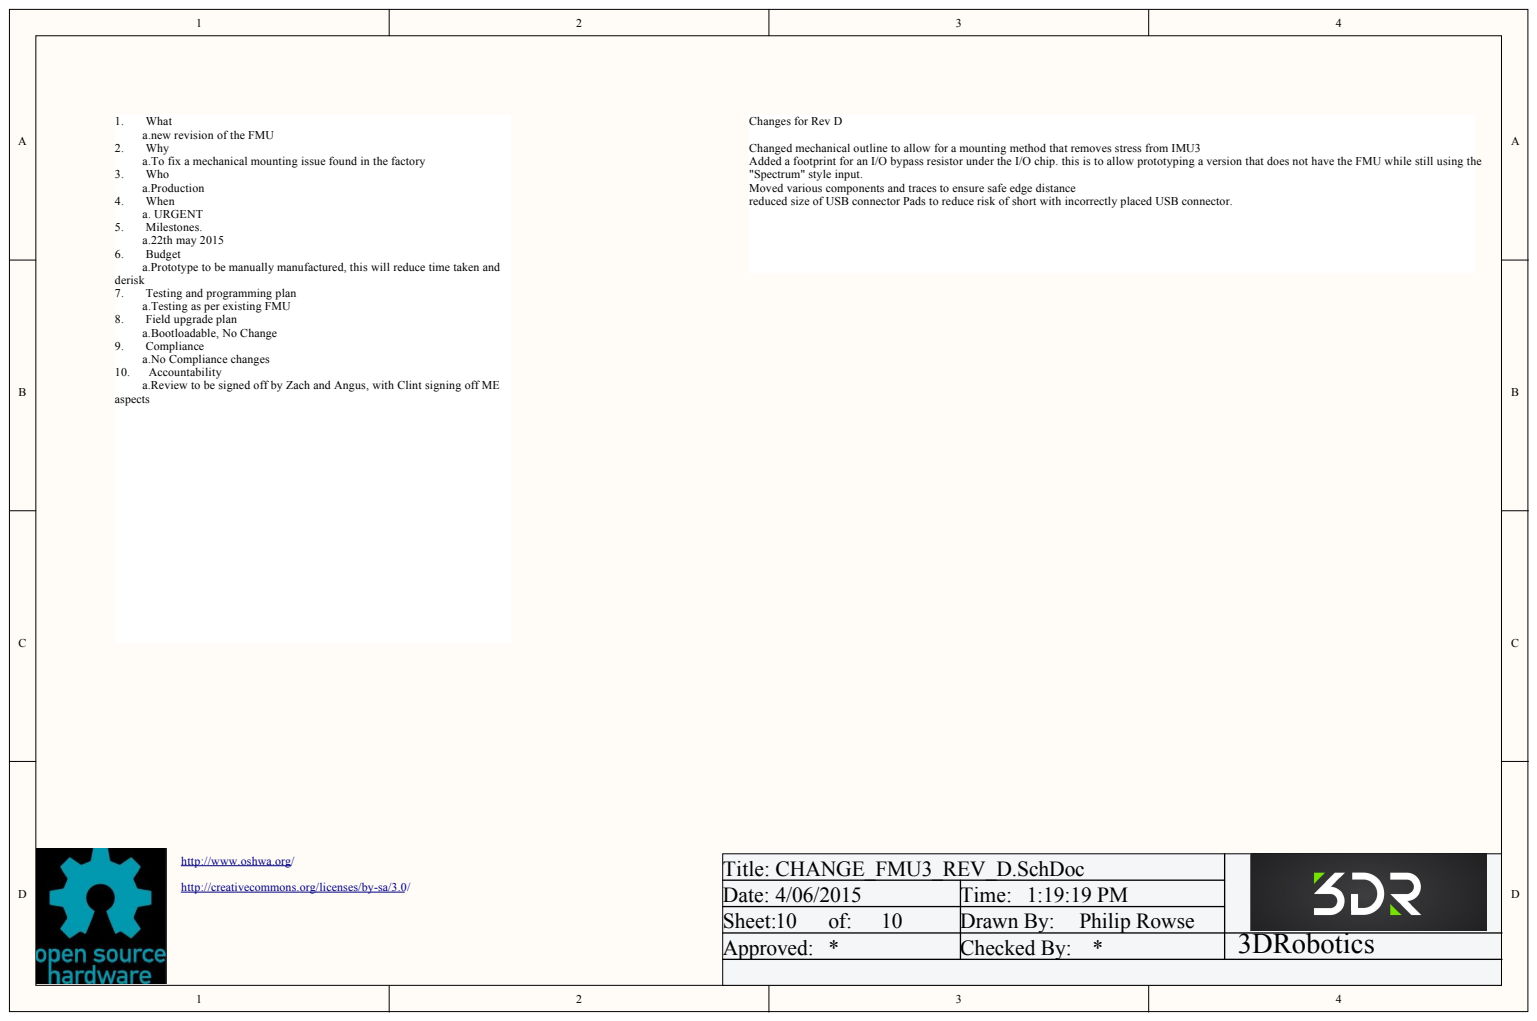
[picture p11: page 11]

1. What
a.new revision of the FMU
2. Why
a.To fix a mechanical mounting issue found in the factory
3. Who
a.Production
4. When
a. URGENT
5. Milestones.
a.22th may 2015
6. Budget
a.Prototype to be manually manufactured, this will reduce time taken and
derisk
7. Testing and programming plan
a.Testing as per existing FMU
8. Field upgrade plan
a.Bootloadable, No Change
9. Compliance
a.No Compliance changes
10. Accountability
a.Review to be signed off by Zach and Angus, with Clint signing off ME
aspects

Changed mechanical outline to allow for a mounting method that removes stress from IMU3
Added a footprint for an I/O bypass resistor under the I/O chip. this is to allow prototyping a version that does not have the FMU while still using the
"Spectrum" style input.
Moved various components and traces to ensure safe edge distance
reduced size of USB connector Pads to reduce risk of short with incorrectly placed USB connector.

http://www.oshwa.org/

Title: CHANGE_FMU3_REV_D.SchDoc
Date: 4/06/2015 | Time: 1:19:19 PM
Sheet:10 of: 10 | Drawn By: Philip Rowse
Approved: * | Checked By: * | 3DRobotics

http://creativecommons.org/licenses/by-sa/3.0/

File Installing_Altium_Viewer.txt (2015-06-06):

go to http://www.altium.com/altium-designer-viewer
Register for your Free license.

With this license you can use most features of altium within this file, ie, cross probing, viewing etc...

To edit, you will need a licenced version of Altium.

As the FMU is 8 layers, it cannot be made in the free version of Eagle... but I would be happy if someone 
could help with the conversion to any other file formats.

Please contact me by raising an issue here.

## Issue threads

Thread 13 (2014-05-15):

PX4 ESC Design

LorenzMeier, 2014-05-15:
The core dev team is currently working on a STM32 based, UAVCAN enabled motor control solution for multicopters. This will be augmented with CAN based sensors, e.g. for angle of attack.

This is part of the core developers roadmap for PX4:
http://pixhawk.org/roadmap

LorenzMeier, 2015-11-05:
And its done!

Closed 2015-11-05.

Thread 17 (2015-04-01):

Problem with PX4-FMU 1.7.1 sch file

touma-setsuna, 2015-04-01:
Hi, I'm trying to make a px4 fmu board for my fixed wing. Now I met some problems with the .sch file. In the latest PX4 FMU 1.7.1, what's the value of RN1 (CTS 742c083)? I can't find this value in this file or BOM.  It appears to be a current-limit resistor between SPI3 and MicroSD. I wonder If any one knows something about this ?  Thanks a lot .  :-)

Closed 2015-11-05.

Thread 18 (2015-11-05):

Settle connector standards with Dronecode

LorenzMeier, 2015-11-05:
Active discussion on Dronecode mailing list.

LorenzMeier, 2015-11-05:
Most manufacturers have settled for JST SH (what APM 2.x used for GPS and what OpenPilot / Naze, etc seem to use) for that use case. Its cheap, available and “good enough” for a QAV 250 small FPV racing quad. Trying to establish something else seems like an uphill battle, since there is a “standard” already.

For the larger systems I have seen a mix of DF13, JST GH and Molex Clik-Mate. The JST GH is a Clik-Mate equivalent and it should fit the same footprint and plastics:
http://www.jst-mfg.com/product/pdf/eng/eGH.pdf

LorenzMeier, 2015-11-05:
You can compare the 6-pos GH vs the 6-pos Clik-Mate - the deviations I found are in the 0.1 mm range. Footprint seems to match as well, but better check yourself. I checked the vertical footprint we use most.

http://www.jst-mfg.com/product/pdf/eng/eGH.pdf

http://www.molex.com/pdm_docs/sd/5023820671_sd.pdf

LorenzMeier, 2015-11-05:
Molex Micro-Lock would be tiny, but is as expensive as Clik-Mate:
http://www.molex.com/molex/products/family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

pavel-kirienko, 2015-11-05:
For reference, side-entry 4 pin 1.25mm:

* [Molex Micro-Lock](http://www.digikey.com/product-detail/en/5041950470/WM10585CT-ND/4879346)
* [Molex CLIK-Mate](http://www.digikey.com/product-detail/en/5023820470/WM4781CT-ND/2649175)
* [JST GH](http://www.digikey.com/product-detail/en/SM04B-GHS-TB(LF)(SN)%3B-/455-1566-1-ND/807834)

DigiKey is rather irrelevant if large quantities are of interest, but still serves as a good reference. It can be seen that JST GH is far cheaper indeed, and all connectors are stockable even in small quantities.

Using this data and the fact that a certain large manufacturer is reportedly using JST GH, I would pick it, but it's hard to make a decision without studying the options up close.

proficnc, 2015-11-05:
As things have "changed" in regards to the manufacturing here... I am no longer against a change in connector type.  However, the reasons we wanted to move to clickmate included the following...

1. Easier to remove.
2. Secure.

If these goals can be met, then I am happy...

pavel-kirienko, 2015-11-05:
@proficnc I wouldn't even consider an option without some sort of positive lock, luckily JST GH has it so I consider it secure and generally usable (but again, I didn't have a chance to tinker with it myself so I can only guess).

proficnc, 2015-11-05:
Yeah, it looks good...

j3qq4hch, 2015-11-05:
Some pics for comparing
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

j3qq4hch, 2015-11-05:
Source sketchup model can be found here:
ftp://pkir.net/CONNECTOR_COMPARE.skp

j3qq4hch, 2015-11-05:
Looks like JST wins

pavel-kirienko, 2015-11-05:
Thanks Alexander. So far JST GH definitely wins, we're going to order some for evaluation and then I'll report back.

pkocmoud, 2015-11-05:
Nick has tried the GH connector and here are his comments:

-this is the same concept as Molex ClikMate.....the same metal pin, but the better pin guides. To me the GH connector design is better than ClikMate

-the plastic body of the GHs is better designed

-I discussed these GH connectors with Georgi Kasabadjakov - the guru in mold production and his opinion is like mine.

nickarsov, 2015-11-05:
Hi guys,
The GH has one main benefit ( in addition to the better design ) - the metal pins have guides....take a closer look at them and you'll see the better design. Bye bye Molex.....

LorenzMeier, 2015-11-10:
Final vote, please participate: http://doodle.com/poll/ynkumy4u8vrfhhme

pavel-kirienko, 2015-11-10:
Lorenz, I think calling it final might be a bit premature. I don't think all of the people involved in the voting are making informed enough decisions, rather I would expect many participants to vote for their own precious connector type in order to avoid the hassle of transitioning to the new type.

This poll indeed seems like a good indicator of the community/industry's preferences, but I wouldn't trust it to make the final decision.

LorenzMeier, 2015-11-10:
The disclaimer in the TSC announcement said exactly that - it is an additional data point. The final is meant to indicate that this is my last attempt to solicit feedback before making a decision.

ivereninov, 2015-11-11:
Connectors always have been a very tough decision for me. As engineers we always aim for the smallest connector, to make our devices smaller (==cooler),  but they are not always optimal for end users. We feel comfortable with them, because we use them everyday and we adapt.

Some comments about presented options:
1. Still not easy to handle, try to reconnect some of them in -10C during a mission when your fingers freeze.
2. Only 1A in power (in CAN topology that is for all device in the net), limits powering through CAN.
3. Impossible to have nice cable overmolding and cable stress reliefs.
4. None of these 1.25mm connectors are meant to be used for module to module communication, mostly they are designed for use inside consumer electronics enclosures.
5. They have very low resource, mostly 10-20 connections. Design goal is that they survive assembly on the factory and maybe disassembly during service. Not intended to be disconnected often. You can have removable wings or payloads.

There is definitely a need in a tiny connector and JST GH looks like clearly winner here, but most installations nowadays would not require miniaturization as APM is mostly chosen for flexibility, thus more payloads and larger frames.

I think there was enough user feedback about DF13 to consider using a larger connector(2.54mm for example)?

As a compromise, how about we define several types of connectors (Dronecode connector, Dronecode micro connector)?

Since most autopilots will be getting rid of numerous SPI, I2C, ADC connectors in favour of CAN there will be plenty of space left for a larger connector.

LorenzMeier, 2015-11-24:
@ivereninov We will cross that bridge when we get there. I expect that Dronecode will eventually have three tiers:

  * Consumer connectors. Something like JST SH
  * Industrial in-module connectors. JST GH
  * Industrial vehicle-level connectors. Automotive and sealed

We have set the middle tier now and we'll leave the bottom and top tiers open until we *really* have adopted CAN.

proficnc, 2015-11-24:
To be honest, a recommendation here is ok, but the application diversity of these platforms calls for flexibility

Can is Clickmate.... All current can hardware developers and manufacturers agree... And as its new, that's cool to be a "standard" but everything else has other things to concider.

pavel-kirienko, 2015-11-25:
@proficnc I think it's not too late to move CAN to the new connector, bridging the transition with adapter cables. Board manufacturers can also win from the fact that this new connector is footprint compatible with CLIK-Mate.

pavel-kirienko, 2015-11-25:
I have evaluated JST GH and couldn't find any issues with them. I agree with Nick's assessment above.

proficnc, 2015-11-25:
IMHO, I actually think there are significant benefits to having the CAN connector be different to the other connectors.  It makes it very clear to the consumer what each connector is.

For Pixhawk 2, we are seriously concidering moving back to DF 13's for supply chain reasons, but keeping clickmate for CAN.

I personally love the idea that there would be a standard for certain connectors, and do not object that it is GH. But I think that the realities of usage have not yet really been discussed here.

Why would we make the CAN and I2C connectors the same? By using different connectors, we make it simple for users.

I actually think we need a real meeting on this topic, and to discuss it calmly

LorenzMeier, 2016-01-14:
Thanks everybody for contributing! The first boards with JST GH are fielded now and the connector is the best I've used in years. I'm going to stop lobbying for it now, because any of you working with it will be immediately convinced its totally worth it.

HackInvent, 2016-07-19:
Hi, am sure my question comes late, why didn't we consider Molex Picoblade series in the discussion?
http://www.molex.com/pdm_docs/sd/530470410_sd.pdf

d-skinner, 2016-07-22:
Hi All,

I'm interested in how the dronecode wire colours were selected? Why are we using black for everything that's not VCC??? I know this as be a "standard" for a while but it's always been a little scary to me. It seems a lot nicer to use red for VCC, black for GND and maybe white for everything else (ie. signals)? I only say this from my experience over the years of development that when you need to quickly hook up some electronics for testing it can be useful to simply cut a cable and solder the wires on. Even though you're still going to need to check what's what with the white wires, it would at least make it clear that you're hooking up a power wire (either VCC or GND) rather than a signal wire.

Thoughts?

Closed 2016-01-14.

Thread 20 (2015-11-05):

Pixhawk 2 bundled power supply: Check design

LorenzMeier, 2015-11-05:
The Pixhawk 2 bundled 8S power supply unit we got (prototype) has 1.2V on the output. I would like to understand if this a manufacturing or design flaw, and how we move on from there.

proficnc, 2016-11-08:
this was an issuer with manufacturing.
the voltage divider had been populated backwards.

This design is now defunct.

Closed 2016-11-08.

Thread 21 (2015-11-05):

Pixhawk XRacer: Minimal, ultra-low-cost Pixhawk variant for small drones

LorenzMeier, 2015-11-05:
Working on this with Phillip K. and Nick. Purposefully reduced to the bare minimum to allow a clear product-market-fit for racer pilots. Has CAN in contrast to small other variants like Pixfalcon. Will fill this with feedback and issues as testing becomes available.

kwikius, 2016-05-13:
Is the CAN cable intended to chain in and out of all the ESC's? My personal view is that makes this type of CAN bus architecture too cumbersome for small drones. A star architecture is a more natural fit

LorenzMeier, 2016-05-13:
Its up to you to use a star cabling or not. The stub length certainly allows it.

kwikius, 2016-05-13:
OK.. What is the maximum allowed stub length ( or rough guide to that)

LorenzMeier, 2016-05-13:
CAN standards says 0.6 m per stub, so unless you build a monster drone easy to comply with.

kwikius, 2016-05-13:
OK it is interesting information that it is allowed. My use case was to put arbitrary things, sensors, RC receiver, GPS etc in the wings of an aircraft. The idea is that for high performance soaring that would allow a slimmer fuselage. Anyway I guess this will work fine for racing quadcopters.

Closed 2016-05-13.

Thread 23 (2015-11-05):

Open housing, and foam

proficnc, 2015-11-05:
The housing for Pixhawk 2 is an integral component to to design.  Where do we stand on its inclusion as a PX4 design? The foam as well...

LorenzMeier, 2015-11-05:
Its a good point. We probably should try to provide or recruit someone to provide a reference unit.

pkocmoud, 2016-11-08:
Chatted with @proficnc and this issue is obsolete.

Closed 2016-11-08.

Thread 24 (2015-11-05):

Foamless IMU

proficnc, 2015-11-05:
With the move to the MPU9250, and the potential for high rate reading. The need for a large isolation system is reduced.
Some form of mechanical and thermal isolation is still needed, but we should consider some options here.

pkocmoud, 2015-11-09:
Hi Philip. The biggest complaint I hear about the MPU9250 is the internal magnetometer is difficult to use or is not reliable. The XRacer has a MPU9250 (Gyro/Accel/Mag) + ICM20608 (Gyro/Accel) / HMC5983 (Mag). I am hoping that this will give us the opportunity to validate the usability of the MPU9250. It should be noted that the ICM20608 is a newer version on the MPU6500.

proficnc, 2015-11-10:
Yes, we have the an HMC5983 next to the 9250... So it will be interesting...

Yes, and if the mag in the 9250 doesn't do what we need, the ICM is the logical replacement

pkocmoud, 2016-11-08:
Chatted with @proficnc and this issue is obsolete.

Closed 2016-11-08.

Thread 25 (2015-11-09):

Standardize usage of RTC memory bridge capacitor for Pixhawk series

LorenzMeier, 2015-11-09:
All Pixhawk series boards should buffer the RTC RAM. We have now hard fault logging:
```
[boot] Fault Log info File No 3 Length 3257 flags:0x00 state:1
[boot] Fault Log is Armed
[hardfault_log] Fault Log is Armed
```

Which means even if the whole OS crashes it will power-cycle, offer the last system state for an in-flight restore and then once the system is back up online write the fault to the microSD for post-flight analysis.

LorenzMeier, 2016-01-14:
Done on Pixracer.

proficnc, 2016-11-08:
Done on Pixhawk 2

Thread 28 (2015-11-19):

Debug port: Find pattern which avoid back-powering everything

LorenzMeier, 2015-11-19:

LorenzMeier, 2015-11-19:
The current default wiring is back-powering the MCU and SD card and browns-out the microSD card.

pkocmoud, 2015-11-19:
We will add a 220R resistor between FMU_3.3V and GND to the production changes.

proficnc, 2016-11-08:
sorted on Pixhawk 2

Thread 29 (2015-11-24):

Settle on standard CAN transceiver

LorenzMeier, 2015-11-24:
We should identify the default part.

pkocmoud, 2015-11-24:
When developing the CANESC 1.6 it was suggested that we choose a part which was
ISO 11898-2 compliant. https://en.wikipedia.org/wiki/CAN_bus#Standards Therefore we settled on the Linear LTC2875 http://www.linear.com/product/LTC2875 . It seems to work fine.

nickarsov, 2015-11-24:
Also a very good solution with best performance/price is TJA1051TK3/118

LorenzMeier, 2015-11-24:
@CarlOlsson Sounds like the TJA is your part then.

proficnc, 2015-11-24:
Yes, this is the Transceiver that I am using....

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

CarlOlsson, 2015-11-25:
Ok perfect! Thanks for the info

CarlOlsson, 2015-11-25:
I cant find the TJA1051TK3/118 in the [NXP eagle library](http://www.element14.com/community/docs/DOC-64270/l/nxp-cad-library-for-cadsoft-eagle-software) or the [pixhawk2.lbr](https://github.com/PX4/Hardware/blob/master/pixhawk2.lbr) or in https://github.com/pixhawk/Hardware/tree/master/eagle/libraries/eagle.

If I have not missed it I will create the part but where shall I add it to make it easier for future designers?

LorenzMeier, 2015-11-25:
Pixhawk 2 libraries. The current generation boards are done in Altium.

CarlOlsson, 2015-11-25:
Ok thx!

pavel-kirienko, 2015-11-25:
TJA1051 is good, but in certain cases it is preferable to use a 3.3V transceiver. In this case I would recommend [SN65HVD232](http://www.ti.com/product/sn65hvd232) - it is cheap and automotive grade; the downside is that it's only available in SO8 which is huge.

[LTC2875](http://www.linear.com/product/LTC2875) Phillip mentioned is another 3.3V alternative in a small package, but its cost may be prohibitive.

proficnc, 2015-11-25:
Agreed on the 3.3 vs 5v issue.

May I suggest that rather than trying to define a standard here... We just list devices that have been verified, with their strengths and weaknesses listed?

As long as they perform the job they are required to do, the choice should be up to the needs of the designer.

We should list some tests, ie, is it non blocking when a micro sets pins to locked values etc....  So maybe add a blacklist of parts that we will not accept if proven not to be up to standard

CarlOlsson, 2015-11-26:
I agree.
The reason to why I asked in the first place was that I wanted to use a design already proven to work.
The list so far:
- Olimexino: **MCP2551-I/SN**
- Pixhawk ESC 1.6: **LTC2875**
- Pixhawk ESC 1.4b: **MAX3051EKA**
- s2740vc ESC and XRacer: **TJA1051TK3/118**

LorenzMeier, 2016-01-15:
@CarlOlsson What was the final choice?

proficnc, 2016-01-15:
The final choice was a whitelist and blacklist... As different components may suit different applications.

Anything that is deemed unsuitable should be blacklisted

nickarsov, 2016-01-15:
To me, the white list currently looks like:
TJA1051TK3/118
LTC2875

proficnc, 2016-01-15:
Agreed

LorenzMeier, 2016-01-15:
Thanks for the feedback Phil! I'll get that into the Dronecode wiki. What voltage are these designed for - 3.3V?

proficnc, 2016-01-15:
The Can side is always 5v, but the secondary on the TJA105 is 3.3v

Need to check the others

This is the one I am using now for all new designs

LorenzMeier, 2016-05-10:
Noted here: https://wiki.dronecode.org/workgroup/connectors/start?&#can_tranceivers

Closed 2016-05-10.

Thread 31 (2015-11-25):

When to terminate the CAN Bus?

CarlOlsson, 2015-11-25:
*"According to ISO 11898, placing the termination resistor on a
node must be avoided because the bus lines lose termination if the node is disconnected from the bus.”*

As far as I understand the s2740vc ESC:s are internally terminated. Doesn’t this mean that they “have” to be placed at the end of the bus?

pavel-kirienko, 2015-11-25:
To the best of my knowledge s2740vs do not terminate the bus, it would be pointless. Generally you have to use a termination plug like [this one](http://nicadrone.com/index.php?id_product=54&controller=product).

CarlOlsson, 2015-11-26:
Ok thanks, as you said, makes more sense

Closed 2016-06-16.

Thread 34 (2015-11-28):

Pixracer: Do not expose interverted and non-inverted signals for FrSky bus

LorenzMeier, 2015-11-28:
We should only expose these once to save board space. They can't be used in parallel, and its better if users get two different cables, which will make it obvious they will have to decide.

We should also work out what the correct cabling to FrSky is.

LorenzMeier, 2016-01-14:
@nickarsov @pkocmoud Done, thanks!

Closed 2016-01-14.

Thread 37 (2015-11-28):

Check is we can move the IO interface port to USART1 or UART8

LorenzMeier, 2015-11-28:
We can access the HW flow control pins of USART6 on larger packages and hence should see if we can free that port.

LorenzMeier, 2016-01-14:
Not required.

Closed 2016-01-14.

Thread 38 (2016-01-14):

Pixracer: PPM pin output resistor value

LorenzMeier, 2016-01-14:
@nickarsov @pkocmoud @kd0aij I'm tracking this here for now. We can't seem to be using 470R for the backwards direction, we need to use something with much higher resistance, e.g. 1.5K or 2.2K. We need to try it against real hardware.

Can you please attach (just drag images onto the text pane to attach) scope shots of the port?

pkocmoud, 2016-01-15:
DSM 470R
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

pkocmoud, 2016-01-15:
DSM Open Resistor
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

pkocmoud, 2016-01-15:
DSM R200 = 1.8K
(RC and Bind works)
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

pkocmoud, 2016-01-15:
DSM R200 = 2.2K
(RC works and Bind does not)
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

pkocmoud, 2016-01-15:
My suggestion is continue testing with the 1.8K resistor.

nickarsov, 2016-01-15:
So, PPM ( PWM->PPM converter ) works with both 1k8 and 2k2, but 2Y must be LOW ( FMU_RC_OUTPUT must be LOW when using with PPM/Spektrum sat ).

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

LorenzMeier, 2016-01-15:
As Nick says we have to re-test to make sure we can reach 3.3V and 0V. In your scope shots the signal is still at 1V, which seems a stretch for robustness.

nickarsov, 2016-01-15:
Lorenz, can you please fix the FMU_RC_OUTPUT = LOW when using PPM/Spektrum. With this fix I'm sure we can go with 1k8 without problems.

LorenzMeier, 2016-01-15:
I'll leave that to Mark to not confuse your workflow. @kd0aij Can you test that with Phil / Nick? Please re-share the analyser shots here so we can do a final review.

kd0aij, 2016-01-15:
@LorenzMeier We're seeing good logic levels on RC_INPUT with a variety of receivers and R200 as a 1.8K pulldown. But DSM binding is working only with clones, not authentic Spektrum satellites. The timing precision of the bind pulses is poor with fmuv4, but good with fmuv2. I'm confused by that, since it looks like the same method is being called in both cases (dsm.c::dsm_bind)

kd0aij, 2016-01-15:
latest test config is here: https://github.com/PX4/Firmware/issues/3513

LorenzMeier, 2016-01-16:
@kd0aij @pkocmoud @nickarsov Per my last discussion with Phil we propose to abandon S.BUS output and pairing for the first rev. Both are fringe use cases which have *not* been promised to the community or customers.

LorenzMeier, 2016-01-26:
Fixed in final HW rev.

LorenzMeier, 2016-08-04:
@pkocmoud What did you end up using in the final HW rev on populated boards? Did this get reflected into a design revision on the schematics for R12 (or whatever the one is which is in production)?

pkocmoud, 2016-08-04:
R12 this resistor is not populated. The downside is R12 boards cannot command the Spektrum satellites into bind mode. R14, the output was re-routed to not go thru the signal inverter. DNP is listed on both R12 and R14 schematics for the resistor in question.

Closed 2016-08-04.

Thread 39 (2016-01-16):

Pixracer: S.PORT output

LorenzMeier, 2016-01-16:
@kd0aij @pkocmoud This is to track the S.PORT electrical spec.

LorenzMeier, 2016-01-16:
@kd0aij If you agree my first proposal would be to hook it up and see how the signal behaves, then to read the data on the bus to ensure we get everything on our side, then write something after the frame from the RX (just anything so we see if the signal looks good).

That would be enough to call the hardware good. Sending real sensor data (like battery voltage) is a bonus.

kd0aij, 2016-01-17:
frsky_telemetry daemon on port ttyS6 is sending altitude (looks like lpos.z) successfully to a Taranis X9D through a D4R-II RX
That's with the PixRacer TX connected directly to the D4R RX, of course. PixRacer RX was not connected for this test.

pkocmoud, 2016-01-17:
With a diode connecting the TX to the RX from the PixRacer, the Voltage of the TX signal is 2.4v. The waves appear very square. Mark is proceeding with updating the frsky_telemetry to use the X-Type signaling.

pkocmoud, 2016-01-17:
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

LorenzMeier, 2016-01-17:
@kd0aij @pkocmoud Do you have an update on the status? I'm getting more and more user requests, including questions for where the S.Port cable is.

pkocmoud, 2016-01-18:
The cable is a tough question. We provided the cable we did so it could be spliced as the user requires. FrSky uses one 4 pin connector on the X series receivers, yet on the connected FrSky devices use a standard 3pin .1 Servo style female connector. I think the best approach is I will order both cable and offer to sell as accessories on the site.

kd0aij, 2016-01-18:
@pkocmoud My signals (with RX connected directly to TX) look better than yours. I suggest you test with the diode shorted to see if I'm right.

kd0aij, 2016-01-19:
WIP on SmartPort telemetry daemon is here: https://github.com/PX4/Firmware/pull/3529

LorenzMeier, 2016-01-20:
A couple of observations: This here would be how to do single-wire properly behind the inverter that we already have:
https://github.com/dword1511/onewire-over-uart

We never have non-inverted single-wire. So we could shut off the the TX line together with the inversion signal and use a block like the one below for FrSky and for S.BUS:

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

kd0aij, 2016-01-20:
"singlewire" there is just a junction? and your intent is to be able to run the uart in full-duplex mode also?

I think Phil's goal is change R13 so that it's an optimal implementation, but that depends on whether we require both full and half duplex or just half duplex

LorenzMeier, 2016-01-20:
The link in my post above has the full schematic for "SINGLEWIRE".

LorenzMeier, 2016-01-20:
We only have two configurations:
- Non-inverted UART
- Inverted, single-wire UART

I would not be aware of anything in the RC space that would depart from that scheme.

kd0aij, 2016-01-20:
clarifiying the RC space requirements
1) non-inverted UART (RX only): DSM, STM24, SUMD
2) non-inverted UART (bidirectional) through inverting transceiver: SBUS2 (RC in and telemetry out) and SmartPort (poll in and telemetry out)

davids5, 2016-01-20:
I sure am lost in the words.

How about a **requirements** chart (rich spread sheet) that list all the Protocols and has TX, RX listed and the sense with respect to the CPU.

Like:

PROTOCOL |TX (out)|RX(in)|Circuit
------------ | -------------| -------------|---------
TTL Serial|NON-INVERTED|NON-INVERTED|insert image
INVTTL Serial|INVERTED|INVERTED|insert image
DUM| NC|NON-INVERTED|insert image
DEF| NON-INVERTED|NC|insert image

Then add a column for existing interface solution for only that protocol where it says insert image

davids5, 2016-01-20:
Also it would be nice to have bit rates listed too.

kd0aij, 2016-01-21:
good idea. The requirements must specify precisely which protocols must be supported by the hardware and which are mutually exclusive (one element of a set must be chosen and whether that selection must be made at compile time or deferred to run time).

If this isn't already written down, I suggest that the hardware should support CPPM, DSM or SBUS input (selected at runtime based on which decoder succeeds), and SmartPort output compiled in. Nothing else. Once this is agreed upon, the remaining tasks become well-defined.

LorenzMeier, 2016-01-21:
@davids5 The key is to have ownership here. Its not a technical problem. I gave you the complete spec already (we need plain serial or inverted single-wire serial and nothing else). @kd0aij If you would like to create the complete list (which will reduce to just the two things I provided above again) I'm fine with it, but I want to know who assumes responsibility in validating the interface. I feel you're up to speed now so you could certainly handle that.

@davids5 Its not necessarily helpful to discuss the full specs with everybody, since they only make sense if everybody understands virtually every radio protocol out there. We don't have the luxury to be able to train several people in all those, and so the table will remain meaningless.

kd0aij, 2016-01-21:
And the R12 hardware can provide the bidirectional 1-wire support on the USART8 pins (with the right cable) with no hardware change at all. Further testing of https://github.com/PX4/Firmware/pull/3553 is invited.

I'll look further into singlewire mode and the circuit recommended by the Taulabs here: https://github.com/TauLabs/TauLabs/wiki/User-Guide:-FrSKY-S.PORT-telemetry
especially since they mention using a direct connection to the TX pin on STM32F3. Perhaps that would free up a couple of GPIOs

LorenzMeier, 2016-01-21:
The F4 has no hardware inverter. It's older than the F3 family.

LorenzMeier, 2016-01-21:
Can you put up a photo in the PR of the cable so people can rebuild it and know where to connect it on the RX?

kd0aij, 2016-01-21:
Thanks, I hadn't looked at the F3 yet.
:) you don't want to see my cabling. Bare wire clamped together with logic analyzer probes.
@pkocmoud Did you make a diode-free cable yet?

pkocmoud, 2016-01-21:
I did, it works fine. I asked Nick to post a graphic.

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

nickarsov, 2016-01-21:
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

kd0aij, 2016-01-21:
So if we don't change the smartport logic of R12 at all, we can also use it as a non-inverted TTL uart port.
Because we have a pin dedicated to the FrSky_inv control. That gives the FrSky I/O pins an additional function which is not yet recognized by the firmware. As long as the 1K series resistors don't conflict with this other function, that port is fine.

nickarsov, 2016-01-21:
Agree......+ if we separate the PB0 and PC7, and connect PB0 directly to RC_INPUT, our RC_INPUT port is fine too. That means we can proceed with R12 with just fix of a track.

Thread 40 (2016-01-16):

Pixracer: Package content

LorenzMeier, 2016-01-16:
@pkocmoud @nickarsov Its not clear what your customers get with each Racer. What exactly is in the box? Which list of cables? Mounting material (the racer frames do not come with any)? Foam?

pkocmoud, 2016-01-17:
1 WiFi Adapter - ESP-01 flashed with MavESP8266

11 Included Cables (All very flexible Silicone):
2 Power Cables - 150mm and 25mm
GPS cable  - 3D Robotics uBlox 5 GPS - 150mm
GPS cable  - Ready to Fly Quad uBlox m8 GPS - 150mm
Buzzer and Safety Switch - 150mm
Telemetry1 Cable (Separate 2.54mm females) - 150mm
Telemetry2 Cable (Separate 2.54mm females) - 150mm
OSD Cable (Separate 2.54mm females)  - 150mm
CAN Cable - GH to GH - 150mm
PPM / SBus Input Cable - 150mm
Spektrum Satellite Input Cable - 150mm

The Following are subject to change.

No Mounting Material is included.

No Foam is Included.

LorenzMeier, 2016-01-17:
It would be great to update the product listing with this and to be more specific from a customer perspective. E.g.: "PPM / SBus Input Cable - 150mm" should become "PPM / SBus Input Cable - 150mm, GH to standard servo connector and single pin (for RSSI)"

The GPS cable should not reference a hardware revision, instead something like: "GPS cable - 3D Robotics GPS module (separate serial and I2C plugs, DF13) - 150mm"

LorenzMeier, 2016-01-17:
What happens if I don't buy a power module from you - how do I get power? Did you consider adding a JST GH to DF13 power cable (replace the long version with that)?

LorenzMeier, 2016-01-17:
What is the "OSD" cable? What is its pinout? Which OSDs are supported?

LorenzMeier, 2016-01-26:
@pkocmoud Product listing still doesn't actually show or list in detail what is included: http://www.auav.co/product-p/xr-v1.htm

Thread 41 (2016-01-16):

Pixracer: Mounting material

LorenzMeier, 2016-01-16:
@kd0aij @pkocmoud @nickarsov The QAV250 doesn't include mounting material for the autopilot. So if you order it and a Pixracer you can't mount it. What were you planning in terms of mounting hardware?

pkocmoud, 2016-01-17:
The users that are buying and mounting this board will typically have their own particular type of mounting or vibration management solution. This is one way they tune their experience. If they want a recommendation from us on this topic, rest assured it will appear in an email or a forum.

LorenzMeier, 2016-01-17:
The difference with your offering with other offerings is that they indeed do not rely on the user to figure things out, but provide a default solution:
http://www.hobbyking.com/hobbyking/store/__67377__Mini_Flight_Controller_Mounting_Base_30_5mm_Naze32_KK_Mini_CC3D_Mini_APM_30_5mm_36mm_.html

LorenzMeier, 2016-01-17:
I'm also confused by your statement regarding the ACSP: You're saying its designed to be stacked, are you really assuming that your users have spacers in different heights available to them?

From a general commercial point of view buying a Pixracer and a QAV250 should result in a flying quad if you want to position yourself as a high-end western provider.

Four spacers cost about $0.40 total. How much is one of your bundled cables?

SimonWilks, 2016-01-17:
Here's a trivial start. Spacers would still be needed, alternatively a smarter case design to take the powerboard too. If a mount isn't made available at least as an option at least spacers would be good as it's not trivial to get a hold of these.

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

Mounted ready to go into a mini flying wing:
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

Sketchup and STL: [pixracer_mount.zip](https://github.com/PX4/Hardware/files/93387/pixracer_mount.zip)

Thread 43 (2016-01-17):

Pixracer: Establish HW test set

LorenzMeier, 2016-01-17:
@pkocmoud @nickarsov Is there something I can help with in terms of the HW test routines? I presume you use something like ```tests sensors``` - what else do you need?

proficnc, 2016-01-17:
You could look at the test suite that Tridge and I (and others) did for Pixhawk 2, it's all open source.

LorenzMeier, 2016-01-26:
@proficnc Indeed. @pkocmoud I've followed the test jig development quite closely, let me know when you want to get up to speed and sync.

@kd0aij @pkocmoud I've fixed the 'tests' command (stack) and it should behave now on master for you.

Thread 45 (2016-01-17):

Find sealed connector standard

LorenzMeier, 2016-01-17:
@proficnc This is to track our discussion about sealed connectors for Dronecode. Feel free to throw in any intermediate results.

ChukRhodes, 2016-01-28:
I've used [Micro-Con-X](http://www.switchcraft.com/Category.aspx?Parent=1147) with good results in most weather. They probably wouldn't do well under water. Easy enough to solder/assemble by hand. And a decent range of panel and cable ends, male and female sockets, solder cup and PCB pins. Not the smallest thing available, but are end-user friendly (for custom cables).

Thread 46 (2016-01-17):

Dronecode power connector recommendations

LorenzMeier, 2016-01-17:
Since manufacturers are also doing power modules and ESCs it would be good if we could identify a low-cost automotive type we can recommend. I think the drone industrial space will need the same kind of standardisation as automotive needed.

For now just looking for recommendations, its too early to try to standardise as we hardly understand the needs and market.

@proficnc Feedback welcome!

Some common types:

  * Hobby connectors like XT60, non-crimpable
  * Professional connectors like Anderson Power Pole: http://www.andersonpower.com/us/en/products/powerpole/index.aspx (crimp able, stackable, not sealed)
  * Automotive sealed power connectors - suggestions?

pavel-kirienko, 2016-01-17:
Hobby connectors need to go (XT60, Deans T, bananas). I would propose the following set of requirements to the *standard power connector*:

- Both board-to-wire and wire-to-wire options should be available
- The connector should be crimpable for manufacturability reasons
- Positive lock
- Availability (should be available from DigiKey)
- Reasonable cost
- It is preferable to have different options for different power levels
- Small pitch

JST J300 could be a good fit for under 15A applications (which is a majority of applications); shame it's hard to stock: http://www.jst-mfg.com/product/pdf/eng/eJFA-J300.pdf

LorenzMeier, 2016-01-17:
Your requirements sound good.

Some starting points for further research (ideally the series would offer sealed and unsealed options, like some automotive series do). Or we pick a sealed and an unsealed, very cheap option (similar to JST GH).

http://www.te.com/usa-en/products/connectors/automotive-connectors/intersection/hybrid-and-electric-connecitvity-solutions.html

http://www.delphi.com/manufacturers/auto/connection-systems/standard-automotive-connection-systems

http://www.molex.com/molex/products/group?key=sealed_connectors&channel=products

LorenzMeier, 2016-01-17:
Equipment supplier pages also help, since they show what's currently being used in the industry:
http://www.waytekwire.com/products/11/Multi-Pin-Connectors/

SimonWilks, 2016-01-17:
Some thought should be given to what the "majority" would be. An F450 flying around normally for example already draws over 15A. Knowing what burst currents they can handle would be useful too.

Looking at some of Mark's logs he seems to have a steady draw of around 10-12A on a 250 already.

F450: http://logs.uaventure.com/view/GEgZgnMSKbHQMpRePVSo6m#Power_PLOT

boosfelm, 2016-01-17:
I agree to @pavel-kirienko requirements except for the current. We have been working with [Anderson Power Poles] (http://www.andersonpower.com/us/en/products/powerpole/index.aspx) for two years now and made only good experience, also meeting all the requirements stated. Depending on the crimp they are rated to 30 or 45A so it would solve for @SimonWilks as well. Also stackable and extendable is nice, 2 connectors DC and 3 from ESC to motor.
Only about price I could imagine there are cheaper solutions.

LorenzMeier, 2016-01-17:
@boosfelm Thanks! I think we can recommend the Anderson series for development vehicles, but we need to find a standard which is really cheap at quantity.

pavel-kirienko, 2016-01-17:
Let us define possible use cases before continuing. As I see it:

- **Main power supply connector**, e.g. battery to a power distribution unit. This connection obviously requires the highest current capacity. It should be either a two power pins connector, or, if we want smart batteries, two power pins plus at least three more pins for the I2C interface. The limiting factor here is probably poor availability of such combined connectors (high-power + signal pins). Wire-to-wire types are not required for this use case.
- **ESC power input connector**. Two pins, lower current capacity (this is where 15A covers vast majority of applications).
- **ESC to motor connector**. Three pins, same current capacity a above.

nickarsov, 2016-01-17:
Hi guys,
For power/signal connector combos, have a look at Molex , Amphenol and Harwin. Such connectors can't be cheap.
Some links:
http://www.molex.com/molex/products/family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
https://www.harwin.com/connector-products/browse-products/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

LorenzMeier, 2016-01-17:
@nickarsov It doesn't have to be cheap, but cost-effective. That certainly exists in the automotive and industrial sector, because both of these are cost-sensitive.

proficnc, 2016-01-17:
The two suggestions from nick are among my favourite, other than the cost.  However, is there any reason we couldn't get a customised connector? Volume is key...

For the ESC, we are dealing with CANx2 + power, on 1 end, and 3 phase + a potential hall sensor out the other end.

The other thing to look at, is waterproofing.

A standard here would be nice,

pavel-kirienko, 2016-01-17:
> For the ESC, we are dealing with CANx2 + power, on 1 end

I am strongly against joining CAN with power on the same connector. First, it adds yet another connector type for CAN (we already have at least three, let's hope vendors converge to JST GH sooner than later); second, it requires manufacturing of custom harnesses because daisy chaining will not be possible.

CAN should be kept separate from power.

proficnc, 2016-01-17:
While I agree with the sentiment of what you are saying, there is a need for a waterproof, compact single connection method.

I highlight that, as there is never going to be a one size fits all here.

We need to realise that these systems are not only being used in 250 racers and DIY gear, but also in commercial Aviation grade applications.  In these applications, custom wiring looms are perfectly acceptable.

This would be highlighted in the automotive world, there is no defined CAN connector, in fact, nearly every sensor has a different connector.  While I understand that is not where we want to go, finding a connector that is designed for harsh environments, for power, and for can, is critical.  But having 4 connectors for a redundant CAN setup, is most likely not feasible for most applications.

For a general standard, the GH is fine, but for commercial exposed applications, both power and CAN must be ip68

proficnc, 2016-01-17:
For general battery power, the XT90-S is nice.

In reality, I again think that we should divide this into purposes...

Clearly Solo has a power connector that suits it's needs... We won't be attempting to standardise OEM's

What we are trying to standardise is the DIY market only, is that a safe assumption?

From that point of view, I am all for the xt60 and xt90 power, and GH for CAN...

But let's also list options for the applications that fit outside those goals.

pkocmoud, 2016-01-18:
While the XT60 are very prevalent, I find that some become very difficult to separate and this can lead to wire / solder joint fatigue on what ever connection is serving as strain relief. I really like the Traxxas RC car connectors https://traxxas.com/products/parts/accessories/highcurrentconnector but they are proprietary and expensive.

j3qq4hch, 2017-04-20:
How about some *fir connectors from Molex? Like [megafit ](http://www.molex.com/pdm_docs/ps/PS-76823-100.pdf)or [ultrafit](http://www.molex.com/molex/products/family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)

They have a lock, they have a key, they are through-hole, so very durable and robust. If 16 or 23 amps per pin is not enough - lets use several pins. They are also crimpable. The only thing I am not sure about - wire-to-wire connection with these.

EShamaev, 2017-04-26:
my few cents:

for wire-to-wire I would consider D369 series from Deutsch (TE): http://www.ttieurope.com/docs/IO/29687/TE_Deutsch_369_Series_Product_Guide.pdf

As for PCB, my choice is Harwin (while not cheap though):
https://www.harwin.com/products/M80-5000000M5-02-333-00-000/
It also comes as combined power/signal:
https://www.harwin.com/products/M80-5L10405M5-02-333-00-000/

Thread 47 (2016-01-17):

Pixracer R13

LorenzMeier, 2016-01-17:
@pkocmoud @nickarsov @kd0aij This is to discuss schematic revision 13.

[PIXRACER-R13.pdf](https://github.com/PX4/Hardware/files/93463/PIXRACER-R13.pdf)

[Pixracer_RC13_CEO_report.pdf](https://github.com/PX4/Hardware/files/93465/Pixracer_RC13_CEO_report.pdf)

LorenzMeier, 2016-01-17:
@nickarsov The issue with the S.BUS inverter (as far as I could see) is that its not bi-directional. So we wouldn't be able to pair or do S.BUS2 telemetry.

nickarsov, 2016-01-17:
The changes are on pages 2/5 and 3/5. PB0 hs been separated from PC7.
The new labels are: PB0 = FMU_RC_INPUT_TIM and PC7 = FMU_RC_INPUT_SER
1. PPM:    RC_INPUT -> FMU_RC_INPUT_TIM
2. BIND:    PB0 becomes GPIO, HIGH for 100ms, then pulsing 3 active low pulses 50us each, then at least 10ms high, then PB0 must be either configured as input or as 3-stated
3. Spektrum/SBus are read via U1203 to FMU_RC_INPUT_SER ( PC7 ) and the inversion of the RC_INPUT signal depends on SBUS_INV ( PC13 ). Inversion is with SBUS_INV = 1.

kd0aij, 2016-01-17:
@LorenzMeier This is intended to be the optimal electrical config with abandonment of bidirectional SBUS support. I think it should allow proper DSM binding though, using PB0 as I/O

nickarsov, 2016-01-17:
Lorenz, can't we use FrSky inverter ( U1202 ) for?

LorenzMeier, 2016-01-17:
@kd0aij It just seems that we will continue to see more single-wire implementations and should position ourselves to be able to do inverted and non-inverted single wire reliably, without strings attached. For RC input we then could connect the TX pin only and use the STM32 in single-wire mode, for FrSky the cable could just pick the TX line and we can do the same in SW.

kd0aij, 2016-01-17:
I believe R13 is an interim (1 batch) solution to go into production ASAP. Right Phil?
Longer term, the question is whether both S.port and SBUS2 are both compatible with the Maxim 1-wire spec. Are there any 1-wire bidirectional buses (yet) which are non-inverted? Since we're short on GPIOs, it would be nice if the answer is no.

kd0aij, 2016-01-17:
I need to look at the STM32 USART single-wire mode. Assuming it turns the IO pin around only when transmitting it should be the ideal solution. Will hopefully be able to do that while debugging the SmartPort code.

LorenzMeier, 2016-01-17:
No you won't, because its only using the TX pin. Which will be blocked by the current unidirectional inverter. I guess you understand now what I mean.

kd0aij, 2016-01-17:
Oh, I knew that :) But I should be able to breadboard it using a telem port.

nickarsov, 2016-01-17:
@Mark: "Are there any 1-wire bidirectional buses (yet) which are non-inverted?"
Yes, there are such - DS2480B, which is an old Dallas Semi chip, but it seems it is still in production.

kd0aij, 2016-01-17:
Is that something an autopilot would need to support?

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

nickarsov, 2016-01-18:
Hi guys,
Here is the sch which seems to fulfill all requirements for PPM, Spektrum, Spektrum Sat, SBus I/O, S.Port, SBus2. A truth table integrated. Please check and confirm.

https://drive.google.com/file/d/0BwGTTqZqRwPLVGVqRUl2bmNHeDA/view?usp=sharing

Unfortunately I'm not allowed to upload PDF files here. Also I can't find the Pixracer folder in https://github.com/PX4/Hardware/

nickarsov, 2016-01-18:
The truth table was fixed and the link has been updated.

LorenzMeier, 2016-01-18:
As of now there is no single wire bus which is not inverted. I can see where you are going with this question. But we don't need a tri-state inverter if it has auto direction sensing.

nickarsov, 2016-01-18:
We need a non inverted Spektrum signal.

kd0aij, 2016-01-19:
Maxim's 1-wire electrical spec:
https://www.maximintegrated.com/en/app-notes/index.mvp/id/214

LorenzMeier, 2016-01-26:
Closing, as we have all this now in R14.

limhyon, 2016-08-23:
I am now testing with R14, still I had a binding issue of DSMX receiver.
Any comments? Also, I couldn't find RC_DSM_BIND parameter when I use Pixracer.

pkocmoud, 2016-08-23:
What flight code and version are you testing with?

titeuf007, 2017-05-20:
hey nick
where we can download  the latest r14 file?
i would like to make my own pcb and soldering by myself but i can t arrive to find them
sorry for my english i am french

Closed 2016-01-26.

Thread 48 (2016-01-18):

Include microSD card in Kit

LorenzMeier, 2016-01-18:
@pkocmoud @nickarsov APM and PX4 both boot into "debug" mode without the microSD card inserted. So unexperienced users who do not insert a card will not be able to connect to the board.

Which essentially means you need to bundle one, because the product is non-functioning without. Hobby king and 3DR both include a card in their default kits.

pkocmoud, 2016-01-27:
This is done. All new orders will include an 8GB Class 4 microSD card.

olibye, 2016-04-13:
I ordered my pixracer via AUAV on 12 March 2016 received it **without** a microSD card.

Closed 2016-11-08.

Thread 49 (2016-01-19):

Pixracer: Potential power sequencing issue on GPS port

LorenzMeier, 2016-01-19:
@nickarsov @pkocmoud The airspeed sensor browns out on boot. The most likely reason is that the power sequencing goes bad during boot.

It only happens when powered through battery, it doesn't happen when powered through USB.

How does the 5V rail plot look like on boot? Please do not offer any judgements, I just want to see the real data. 3 plots:

1) USB power applied
2) Battery power applied
3) A sequence of wiggling the power connector of the battery

LorenzMeier, 2016-01-19:
So it seems like connecting battery "kills" the sensor. Which seems absurd.

Maybe the device went into a bad state when we powered it reverse.

tumbili, 2016-01-19:
Correct, having usb connected the driver works. Connecting power without removing the usb cable kills the driver.

pkocmoud, 2016-01-19:
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

Power Up using Battery, connecting and disconnecting USB, Battery remains connected until the end.

LorenzMeier, 2016-01-19:
@pkocmoud It would be great if you could try to repro with one of these: http://www.hobbyking.com/hobbyking/store/%5F%5F62752%5F%5FHKPilot%5F32%5FDigital%5FAir%5FSpeed%5FSensor%5FAnd%5FPitot%5FTube%5FSet.html

pkocmoud, 2016-01-19:
"repro"? I have the 3DR Version to test with.

tumbili, 2016-01-19:
@pkocmoud That would be great.

pkocmoud, 2016-01-19:
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
Recorded while loaded with Master.

pkocmoud, 2016-01-19:
No Brown Outs Detected. The PixRacer power supply is solid during our tests.

LorenzMeier, 2016-01-19:
@tumbili If you comment out this line, does it work for you?
https://github.com/PX4/Firmware/blob/0e0c1302e41abc75e83bd3b0a324bead952f8a16/src/drivers/meas_airspeed/meas_airspeed.cpp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

tumbili, 2016-01-19:
@LorenzMeier same thing

LorenzMeier, 2016-01-19:
Odd. It has to be somewhere there.

LorenzMeier, 2016-01-20:
So my 2nd board has an all working sensor. We have now 3 boards:

1): 0-1.8V on the 5V rail
2): Romans board: 5V on GPS rail, but no airspeed sensor signal when powered via the 3DR power module
3): Completely working when powered at 5.3V through a lab power supply

The only thing I haven't tried yet is what happens when the sensing / ADC pins are active, as I have no power module.

I certainly have a bad board, not sure yet about the causality of the other two items.

tumbili, 2016-01-20:
@LorenzMeier Is 5.3 a magic value? Does is also work with 5V?

LorenzMeier, 2016-01-20:
Your power module is outputting 5.3V. Which is why I chose it.

nickarsov, 2016-01-20:
Yes, it works with 5V too, because the USB can't supply 5.3V

LorenzMeier, 2016-01-20:
Nick, rather than speculating it would be good if you could work out how I can return the electrically bad board to your for inspection.

nickarsov, 2016-01-20:
Lorenz,
Speculating with what...I just answered to Roman.
And yes, you can return it back to me for inspection at:
Nick Arsov
8 Konstantin Irechek str., bl.1
4700 Smolyan
Bulgaria

LorenzMeier, 2016-01-20:
Thanks, will do! I'm closing this as it seems board-specific.

LorenzMeier, 2016-01-20:
@nickarsov the part you identified has 5V on one side and 0V on the other.

LorenzMeier, 2016-01-20:
Soldering looks sketchy. I will rework it later today or tomorrow.

LorenzMeier, 2016-01-26:
This was in fact the airspeed sensor. Still have one board with 1.8V on that port, but that is probably manufacturing QA. Replaced with: https://github.com/PX4/Hardware/issues/55

Closed 2016-01-26.

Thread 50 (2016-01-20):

Pixracer GPS power port: 1.8V output

LorenzMeier, 2016-01-20:
@pkocmoud @nickarsov @kd0aij I'm measuring 1.8V output on the GPS power port with just the airspeed sensor attached. Can you confirm that? I'm measuring 0V with nothing attached.

nickarsov, 2016-01-20:
Lorenz, which cable do you use as GPS cable has been totally swapped - both GPS connector and I2C connector. I already notified all users about. Can you send a screenshot of the wiring?

LorenzMeier, 2016-01-20:
Its not the wiring, I measured the connector pins. I confirmed that my 2nd board provides 5V, so I got a bad board.

LorenzMeier, 2016-01-20:
Where was the diode that was the wrong way around? Can you mark it in the layout?

nickarsov, 2016-01-20:
There is just a resettable fuse between 5V and VDD_5V_PERIPH. Does it get
hot?

2016-01-20 11:14 GMT+02:00 Lorenz Meier <notifications@github.com>:

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

nickarsov, 2016-01-20:
Picture attached

2016-01-20 11:15 GMT+02:00 Lorenz Meier <notifications@github.com>:

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

nickarsov, 2016-01-20:
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

LorenzMeier, 2016-01-20:
Components on the working and non-working board are all oriented exactly the same.

nickarsov, 2016-01-20:
Maybe the fuse FR101 gets overloaded by some reason...
What is the voltage on its pads?

pkocmoud, 2016-01-27:
This appears to be a defective board. Please close this issue unless other examples appear.

Closed 2016-11-08.

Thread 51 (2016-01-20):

Pixracer: Voltage / current sense pins are inverted

LorenzMeier, 2016-01-20:
@kd0aij @nickarsov @pkocmoud The voltage and current sense pins on the power connector are inverted vs. the 3DR power module (and most likely vs. your own power module as well).

Correct pinout:
https://pixhawk.org/modules/pixhawk

Your pinout:
https://pixhawk.org/_media/modules/pixracer-rc12-12-06-2015-1330.pdf

Note how voltage and current are swapped.

LorenzMeier, 2016-01-20:
@kd0aij I pushed a commit to master addressing this. Its still extremely problematic as it departs from the Dronecode spec.

LorenzMeier, 2016-01-20:
Never mind, I confused it. On re-checking it seems correct.

Closed 2016-01-20.

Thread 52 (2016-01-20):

Pixracer: PB0 (PPM in) should use RC_INPUT, not FMU_RC_INPUT

LorenzMeier, 2016-01-20:
@nickarsov The connection to PB0 should be straight from the raw and non-inverted signal (RC_INPUT), not from behind the inverter.

Independent on how we do the new inverting circuitry that pattern will allow Spektrum binding.

nickarsov, 2016-01-20:
Exactly...I have already separated the two lines in RC13 and RC14

LorenzMeier, 2016-01-26:
Done.

Closed 2016-01-26.

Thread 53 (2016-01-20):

Pixracer: Clarify ACSP4 scaling for voltage and current

LorenzMeier, 2016-01-20:
@nickarsov What is the full-scale from 0-3.3V on the voltage and current sense lines? E.g. if the voltage is 3.3V on both lines, what voltage and what current is the sensor seeing?

Note that you need to have the *same* scaling for both power modules, as your users will get terribly confused else. You only should offer a different scaling range for specific sub groups, e.g. very large airframes.

pkocmoud, 2016-01-20:
The resistor divider is 13k7:1k1. The VMax is 42v.

 42V/14.8*1.1 = 3.12V

The IMax current is 120A (Cooling required above 80A).

120*0.00025*110000/1000 = 3.3V

LorenzMeier, 2016-01-26:
Done

Closed 2016-01-26.

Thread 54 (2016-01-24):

Pixracer: FrSky Telemetry cable

LorenzMeier, 2016-01-24:
@kd0aij @nickarsov Do we need to connect the 5V signal to the receiver? That might be problematic and we might want to only connect S.PORT and GND.

kd0aij, 2016-01-24:
I was not connecting 5V from pixracer to the X4R receiver in my testing, except of course via the RC input cable.
Its purpose is to supply power from the RX to sensors on the bus, so the sensors do not source 5V. The S.port + pin on my X4R-SB is connected directly to the + line on the servo bus, so there shouldn't be a problem if the same supply is connected to both pins.

LorenzMeier, 2016-01-24:
No, there would be a massive problem. @nickarsov If you connect the 5V rail you can fry Pixracer if a servo is back-driven (which happens on planes and servo gimbals).

Building drones is an art. The seemingly simple is quite complex to get right.

LorenzMeier, 2016-01-24:
@pkocmoud FYI: You need to ensure your S.PORT cables do not connect the 5V line.

LorenzMeier, 2016-01-24:
We have seen quite a few people connecting servos to the receiver even if connected to the autopilot.

kd0aij, 2016-01-24:
@LorenzMeier Thanks, I see now they are 2 different supplies, and that this would tie the VDD_5V_RECEIVER and VDD_5V_PERIPHERAL supplies together, disabling the back-emf protection provided only for the RX supply.

nickarsov, 2016-01-24:
Don't forget TVS103 !

pkocmoud, 2016-01-25:
The manual is updated.

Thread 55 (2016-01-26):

PX4 Airspeed sensor: Missing level shifter

LorenzMeier, 2016-01-26:
The PX4 airspeed sensor breakout is using a 5V sensor for a 3.3V bus. It can be fixed in two ways:

 * Use a 3.3V model of the sensor and a small ultra-low-noise LDO in front of it. This would be the best solution.
 * Use a PCAxxxx I2C level shifter to shift the 3.3V signal from Pixhawk / Pixracer to 5V on the sensor side. Will likely require pull-ups on the PCA side.

Scope shots and further discussion here:
https://github.com/PX4/Firmware/issues/3544#issuecomment-174732106

LorenzMeier, 2016-01-26:
@tumbili I'm going to fix this for our internal use with a couple of these: https://www.sparkfun.com/products/11955

LorenzMeier, 2016-01-26:
@AndreasAntener @SimonWilks FYI: You can have a few of the ones I'm ordering if you need them.

@tridge FYI: You will want to retrofit your planes with this. I've notified 3DR / HK and other HW manufacturers that the design is flawed. The setup on Pixhawk turns out to be marginal (it kind of works) but any deviation (higher supply voltage, longer cable runs, noise) can turn it from OK to unreliable.

LorenzMeier, 2016-01-26:
Note that I2C is different from UART and other interfaces which apply TTL levels (so < 0.8V is off, > 2.5V is on). For I2C < 30% of VCC is off, > 70% VCC is on. Which means that the ON voltage is 3.5V at 5V supply, making 3.3V just marginal.

pkocmoud, 2016-01-27:
We will have a new airspeed design that include a proper level shifter on board and JST GH connectivity. We also have an i2c hub design based on the PCA9516A which will accept either 3.3v or 5v i2c on each of 4 ports.

proficnc, 2016-02-06:
the correct fix here is to have an LDO on the Airspeed sensor.

running 3.3V around is really bad.

this is what we do in the GPS.  it allows for some noise in the power line, without affecting the system stability.

There is no need for a level shifter here. just follow the correct power setup.

proficnc, 2016-02-06:
ok, so it appears that there may be more going on here.  I have a board with the 3.3v version and another with the 5V version.

to retrofit the 5V version... then use the level shifter, to retrofit the 3.3v version, use an LDO... future designs should use the 3.3V version... and preferably a can interface.

silkstone, 2016-09-15:
@proficnc @LorenzMeier Hi guys, I am failing to get anything to come through the i2c port on my Pixracer - using an active i2c hub and connecting the PX4 digital airspeed sensor and a Ublox Neo-M8N GPS but have never been able to get a GPS lock and the airspeed sensor reads 0.0 with occasional spikes up to 50 m/s etc.

Tried following the conversation above but don't fully understand if this is the same issue that I am facing. Any help would be much appreciated!

pkocmoud, 2016-09-15:
Have you calibrated your sensor?

athertop, 2016-11-11:
How would one determine if a sensor is pixhawk compatible or not?  I have the HK Pilot digital airspeed sensor connected to my pixhawk lite fc in a flying wing. It's about 4 months old. How can I tell if it's producing i2c errors?

pkocmoud, 2016-11-16:
I would start by comparing the sensors model number to the sensors on existing known supported boards. If that is a match then proceed to study the pinout to ensure you are connecting it properly to the flight controller.

With the typical MS4525DO, I run "meas_airspeed info" from the NSH prompt. The i2c errors are listed there.

athertop, 2016-11-16:
So there exists a list of supported sensors? As regards connections, the sensor does work, but after powering the craft (indoors) it sits at about 7km/h, and even if I do the pre-flight reset option it still goes to about 7km/h initially then slowly rises to upto 20km/h - in no wind (indoors). I have ordered a new sensor from auav to see if this will resolve, and have raised a case with HK.

pkocmoud, 2016-11-16:
Are you using PX4 or ArduPilot?

athertop, 2016-11-16:
Ardupilot Plane v3.7

pkocmoud, 2016-11-16:
Have you posted anything on discuss.ardupilot.org? I think there is a way in Mission Planner to read the airspeed sensors status including Temp. I would expect there would be a correlation between the internal sensors temperature and the drift. Not sure why it starts so high though.

athertop, 2016-11-16:
After reading this report here, I presumed it would be down to it being one of the sensors not supporting the 3.3v signal levels, and therefore getting i2c errors. Lorenz in here does mention that the sensors from HK do have this issue and that he reported it. I need to do the test you mention above. Need to figure out what the NSH prompt is :-)

pkocmoud, 2016-11-16:
The issue listed here would cause the sensor to drop out or be missing. Drift is a fairly standard issue with these sensors. Some suggest a warm up period before use.

dagar, 2016-11-16:
I don't think anything is reported over mavlink. On PX4 I'm adding complete logging for differential_pressure and airspeed which includes the driver error count.
Internally you can look at the differential_pressure topic (listener differential_pressure 100).

pkocmoud, 2016-11-16:
I have seen plotted Airspeed vs sensor temp from Ardupilot / Mission Planner that show this data.

dagar, 2016-11-16:
Yes, there's airspeed and temperature, but not the driver error count. At that point the airspeed will also be filtered. Sorry should have been more specific.

j07rdi, 2017-02-09:
Just to let you know guys we have been offering the airspeed with the fix since a few weeks ago: https://store.mrobotics.io/mRo-I2C-Airspeed-Sensor-JST-GH-p/mro-classy-arspd-mr.htm

jliphard, 2017-06-22:
@j07rdi - I bought two of your sensors, and for both of them I see a severe high frequency ripple on pin 2 (VCC) of the actual sensor, a MS4525. Due to ratiometric analog output, any problems with VCC will feed straight through into the output (pin 3), and from then on into the ADC. Could you please circulate a circuit diagram with some specs on what you were hoping for vis-a-vis the quality of your VCC? Correct me if i'm wrong, but after your LDO, (and whatever noise suppression elements you have in there) should VCC not be VERY smooth and within +/- 1% of +5V. The sensor will sort of work, it will just be much noisier than you expected, and, more problematically, the temp compensation functionality internal to the MS4525 may not perform particularly well if VCC is all over the place. The expected signature of this problem, if it's not just me, would be: (1) unexpectedly 'noisy' sensor readings with a periodicity to the noise, and (2) sensors whose thermal compensation is screwed, giving highly variable baselines. If you put up a circuit diagram, I can do a more detailed analysis of the PIX4AIRSPEEDv1.1 PCB.

pkocmoud, 2017-06-22:
@jliphard - The sensor linked by @j07rdi is the [MS4525DO](http://www.te.com/commerce/DocumentDelivery/DDEController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) which is the i2c variant of the MS4525. I think you might be studying the wrong datasheet.

kaklik, 2018-09-10:
Nevertheless, a circuit diagram of the @j07rdi linked sensor will be useful to verify a correctness of the design. The issue should not be closed until the explicitly known and verified design arise.

j07rdi, 2018-09-10:
Hi there,

Level shifter is below the sensor:

[https://store.mrobotics.io/v/vspfiles/assets/images/AIRSPEED_02.jpg](url)

Cheers!

kaklik, 2018-09-13:
@j07rdi
Yes, I saw that promo picture. But it is not equivalent to schematics of level shifting circuit used.

Moreover, the picture contains unsoldered joints with not liquefied solder paste.

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

j07rdi, 2018-09-13:
@kaklik

The huge chip on the upper part is the level shifter. Please grab a multimeter and verify the output voltages if there is any doubts.

Your observation is not accurate, the solder joins have soldering.

pkocmoud, 2018-09-13:
@j07rdi - I think he would like the schematics updated to include the level shifting change.

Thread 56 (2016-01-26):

Pixracer: 3DR Radio serial cable (or HKPilot Telemetry radio serial cable)

LorenzMeier, 2016-01-26:
We need a JST GH to Molex Picoblade or Hirose DF16 cable, straight, 6 pos.

@pkocmoud @nickarsov

pkocmoud, 2016-01-27:
I think the best approach is to solve this with the I2C Splitter that has JST GH, DF13 and Picoblade plugs. ETA is 2/10/2016.

LorenzMeier, 2016-01-27:
They use serial though. So you still need this cable.

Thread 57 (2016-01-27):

Pixracer OEM

Naish88, 2016-01-27:
Hi,
I will like to suggest a new derivative of the Pixracer.
Many people and companies now are building they own mini drones, and for tight integration they want to use the AP as a daughterboard soldered on top of main distribution board. This reduces the size/weight and increases reliability, plus is easy to integrate into products for commercial companies. In concept is like the Pixhawk 2 cube or the VRbrain core.
The main difference, will be the removal of all the connectors, and the use of one side only of the PCB. SD and USB socket can be optional soldered on the underside, or just installed outside the AP module.

Pixhawk 2 won't be available for sale, and VRbrain is closed sourceHW and works on a separate branch of ardupilot/px4, so not ideal.
Anyone else interested in the Idea? I'm happy to work on it.

pkocmoud, 2016-01-27:
Naish88,

Please feel free to start something. I don't think this is the proper place to propose this as it is not an issue. While Nick and I are too busy at the moment, we could contribute in the future.

Naish88, 2016-01-28:
Philip,
Sorry If I posted into the issue section. I was thinking that's the best place where Leonard Nick and you could all read this. Feel free to close this issue.
In regards of the Pixracer OEM, I'm happy to take on the work. I just wanted to verify that everyone is happy and no-one feels like I'm coping someone's design. I will be really glad if any of you will like to help  with suggestions or anything else, also will be really great if Nick will be able to manufacture and sell the boards, as he has already the Pixracer in the pipe.
Also there is any chance I can get the Altium files? Will save me heaps of time, instead of redrawing schematics and verifying footprints. a Github section for the Pixracer Hw will be great.

proficnc, 2016-01-28:
Pixhawk 2 WILL be available for sale!

I am working to secure supplies.

Contact me if you have any questions

Closed 2016-11-07.

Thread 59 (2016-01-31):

FMUv4: Ensure correct power sequencing when powering from USB

LorenzMeier, 2016-01-31:
@nickarsov We should ensure that any full-sized FMUv4 variant the peripheral power rails default to off and can be actively switched on by the autopilot when it has battery power. This is necessary as some USB lines do not allow enough power to supply the full set of peripherals.

nickarsov, 2016-01-31:
Already done in the preliminary sch.

pkocmoud, 2016-11-07:
This was also addressed in the official FMUv4 Standards doc published 4-3-2016.

Closed 2016-11-07.

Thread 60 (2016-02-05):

TXS0108QFN20 bi directional level converter problem with emax escs

dhirajdhule, 2016-02-05:
The old problem with emax and some other escs ([check this thread](http://diydrones.com/forum/topics/getting-pixhawk-to-work-with-emax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)) with pixhawk.
These esc's are loading the level converter and pwm output signal level decreases from 3.3V to ~2.2 V.
The  TXS0108QFN20 seems to have little high output impedance >4K which is creating problems specifically with EMAX escs. Even though Emax guys have admitted that their escs draw extra current, we can look for some other options to use as buffer on pwm output channels. The problem persists even if the escs are not powered which also is obvious.
I tested the controller output before the TXS0108QFN20  and its normal while the buffers output is loaded. Anyway a good signal buffer for output needs very low output impedance.

proficnc, 2016-02-06:
If you look at the latest Pixhawk 2 drawings, you will see this issue has been rectified

Mr-Anderson, 2016-08-16:
I looked at the drawing and could not find a change that would rectify this issue. Could you please point out the change? EMAX is only using a 10K pull down on their signal line which does not seem unreasonable. The currents drawn by the ESC at 3.3V are only 330uA. These ESC's work with almost every other receiver and flight controller on the market. It seems like the PixHawk drive strength is awfully low for an external signal.

proficnc, 2016-08-16:
The TXS has been replaced.  And the resistor values dropped to 120 ohm.

However, I have never seen an installation where this occurs if the ESC is correctly wired.

It is critical that both the ground and signal pin are connected.

MuneebaAsif004, 2022-03-25:
Does anyone know what has TXS been replaced with?

davids5, 2022-03-25:
From FMU V4 and above the TXS0108QFN20 were not used, just 220R series
resistors and TVS. See the last page of
https://github.com/pixhawk/Pixhawk-Standards/blob/master/DS-010%20Pixhawk%20Autopilot%20Bus%20Standard.pdf

The pattern is

Inboard -----220R---+---------------- connector

                                TVS

                                  +

                                  GND

*From:* MuneebaAsif004 ***@***.***>
*Sent:* Thursday, March 24, 2022 5:24 PM
*To:* pixhawk/Hardware ***@***.***>
*Cc:* Subscribed ***@***.***>
*Subject:* Re: [pixhawk/Hardware] TXS0108QFN20 bi directional level
converter problem with emax escs (#60)

Does anyone know what has TXS been replaced with?

—
Reply to this email directly, view it on GitHub
<https://github.com/pixhawk/Hardware/issues/60#issuecomment-1078527717>, or
unsubscribe
<https://github.com/notifications/unsubscribe-auth/AAO3BXNGTL3FOO4US34V5Z3VBUBS3ANCNFSM4B2RXX2A>
.
You are receiving this because you are subscribed to this thread.Message
ID: ***@***.***>

Closed 2016-02-06.

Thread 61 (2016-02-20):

FMUv4: Power sense pulldowns missing

LorenzMeier, 2016-02-20:
@nickarsov On FMUv4 2M pull-downs are missing on the voltage and current sense lines. An unpowered ACSP4 reports 2V.

nickarsov, 2016-02-20:
Lorenz, have a look at the sch ....you'll see R407 and R408......1M resistors

LorenzMeier, 2016-02-20:
Weird - I saw a 2V level on a board which was not connected to battery. I can't repro now though - closing.

Closed 2016-02-20.

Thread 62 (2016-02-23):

Pixhawk VTOL Issue

VagishB, 2016-02-23:
Hi guys,
I am using pixhawk VTOL firmware in my V-tail airframe. Once I switch ON the safety switch, the plane motor is still beeping(I have also BEC in ESC). Could you guys help me?

LorenzMeier, 2016-02-23:
Is your motor connected to AUX5? There should be a standby signal:
https://github.com/PX4/Firmware/blob/master/ROMFS/px4fmu_common/init.d/13007_vtol_AAVVT_quad#L41

VagishB, 2016-02-23:
Yes my motor is connected in Aux 5 only.
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

Closed 2016-05-01.

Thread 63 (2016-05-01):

FMUv4: Add weak pulldown (1M) on analog RSSI line

LorenzMeier, 2016-05-01:
@nickarsov The analog RSSI line should have a weak pulldown. The signal currently idles at 1.5 volt, which is not good. I might be able to do this with an internal pulldown, but I need to check if that's ok / available for the ADC configuration.

pkocmoud, 2016-05-02:
I just want to make sure, it is a trivial change but it deviates from the FMUv1 (PixHawk) standard circuit design.

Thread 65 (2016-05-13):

in PX4FMUv2.4.5.pdf  PA10 should be labelled USART1_RX not USART1_TX

kwikius, 2016-05-13:
In sheet labelled sheet 1 of 12, top left I think PA10 can only be USART1_RX, but is labelled USART1_TX

https://github.com/PX4/Hardware/blob/master/FMUv2/PX4FMUv2.4.5.pdf

davids5, 2016-05-13:
Not sure what you are looking at....

proficnc, 2016-05-13:
Page 1 is the FMU... It is the RX for the IO, and that is exactly how it is labeled

kwikius, 2016-05-13:
Sorry .. Clearly either I am an idiot or the labelling could be clearer :)

davids5, 2016-05-13:
No worries...It has been an issue with RS-232 (EIA) since day 1. If I was "EIA" I would have called it TX_TO_ME and RX_FROM_ME :)

proficnc, 2016-05-13:
That's why I love the SPI method... Master in slave out.. MISO etc...

Every board I lay out, I always panic on this stuff...

That bit could do with an additional net Kable to clear it up.

Closed 2016-05-13.

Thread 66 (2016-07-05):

Pixracer: GPS+Compass cable - needed RX & TX swapping for uBlox m8n

olibye, 2016-07-05:
Hi Guys,
just to let you know that I had to swap the GPS UART RX and TX lines on the PixRacer supplied JST GH to uBlox M8N micro DF13 cable. I found this issue as a result of your excellent wiring diagrams.

This may be specific to this particular component:
https://www.unmannedtechshop.co.uk/mini-ublox-m8n-gps-module-with-compass-for-px4-mini/

pkocmoud, 2016-07-05:
The cables supplied are for specific models of GPS units only. It is not surprising that some level of re-pinning was required. I am glad you got it up and running.

Closed 2016-07-05.

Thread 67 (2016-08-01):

? pixhawk hardware issue or improvement ?

drones-squad, 2016-08-01:
Hy all,
I have recently noticed something strange about the pixhawk 2.4.5 hardware.
One of the sensor on the pixhawk is called a LSM303D ( a 3D magnetometer and accelerometer)
I was looking at the pixhawk schematics that are to be found on github HERE and saw that the sensor surrounding parts are different then what it's manufacturer suggest. ST shows a completely different arrangement for this. I was just wondering why did the people who build pixhawk reduce this surrounding parts or replaced them with other values. I wanted to hear the explanation of this and how it affects or improve the flight controller.
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

Please check the file in attachment.

Greets

apache405, 2016-08-02:
There is a thread for this on drones-discuss as well.

On Mon, Aug 1, 2016 at 12:56 PM, drones-squad <notifications@github.com>
wrote:

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

drones-squad, 2016-08-02:
Hello apache405,

yes but nobody seem to answer ... I contacted David Sidrane and asked me about this issue and suggested to post this here on github. He also has not received any information for now as I am aware

greets

LorenzMeier, 2016-08-10:
The values were chosen to match the requirements of the 2011 version of the data sheet and generalised to reduce the number of values per board. You might want to update the schematic to match the last manufacturer info.

Most importantly you will want to upgrade the sensors, as sensors available in 2011 are now quite outdated.

udawat, 2016-08-10:
A good combination of sensors from ST include the following:
LSM6DS33 (3D Accel + 3D Gyro) as an update to the L3GD20(H) Gyro.
LSM303D (3D Mag + 3D Accel) - Better than standalone magnetometers.
Both support SPI at 10MHz.

Honeywell's HMC5983 is now End of Life part. For a 3D Magnetometer only option, LIS3MDL is there.

LSM9DS1 should not be considered as it is just two sensor dies in a single package (similar to MPU9250 and 9150).

For Pressure Sensor, Bosch BMP280 can be an option. It supports SPI  at 10 MHz. But, its resolution is 20 bits (not sure) as compared to the 24-bit ADC of MS5611.

drones-squad, 2016-08-10:
Hello Lorenz,

You say that the values were chosen to match the 2011 requirements, can you confirm that this issue was also to be found on the more recent boards like 2.4.6 ? If one will change values then I suppose it will have an impact on the sensor / firmware as well ... ?

And can you please perhaps let me know what kind of sensors you are talking about ? I have searched for example for a good mpu6000 alternative but none found. The newer 9060 or 9050 or whatever are all based on the mpu6000 but with far more less capabilities and functions as they are also cheap. The REAL mpu6000 for example is a rather reliable but expensive part. The lsm303d does all not too bad and the L3GD20H is newer then the L3GD20. But then again Please advice if I missed something, there are a dozen of manufacturers out there with thousands of parts.

greets

igalloway, 2016-08-10:
I haven't done a full competitive analysis yet, and there certtainly are
differences (I2C vs SPI) but NXP mix would be:

·        FXOS8700 Mag + Accel with up to 400Hz sampling rate in hybrid mode
(I2C based)

·        FXAS21002 Gyroscope with up to 800Hz sampling rate

·        MPL3115A2 Pressure Sensor/Altimeter with typical resolution of
0.3m at 1Hz

·        Free/Open Source 9-axis sensor fusion for computing orientation

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

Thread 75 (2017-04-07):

Question+possible issue

johnsp1, 2017-04-07:
I assumed this was a 2 layer board looking at the documentation, but I'm seemingly seeing traces that end  at floating vias?

Say perhaps tracing IO-LED_BLUE or IO-LED_AMBER from the smaller F1 ARM to U703? I'm seeing these paths end at vias floating on the opposite side of the board

Apologies for the beginner question, but is the Pixhawk a 4+ layer board?

davids5, 2017-04-07:
@johnsp1,

I am not sure what you are looking at.  Grab a copy of [eagle](http://www.autodesk.com/products/eagle/overview) and [the files](https://github.com/PX4/Hardware/tree/master) and you can see how it is routed.

Closed 2017-04-07.

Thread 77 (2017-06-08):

Zubax Sapog LED package reversed polarized.

taskx6004, 2017-06-08:
I have build a small batch Sapog ESC according to the eagle files, flashed, motor beeps, but the four color LED is not working. after checking polarity i found the original Sapog LED was reversed and hand solded. please check your sch or please update the design library.

or my fab did it wrong, i will double check.

It's a amazing project @pavel-kirienko. Thanks for you effort. I will not sell these boards for profit. I would like to donate samples to people who will investigate how to use SPI-CAN adaptor to get it work on linux, RPi especially.

pavel-kirienko, 2017-06-08:
@taskx6004 thank you for the kind feedback. Make sure to also check out the new reference manual we're creating: https://files.zubax.com/products/io.px4.sapog/Sapog_v2_Reference_Manual.pdf

Calling in @j3qq4hch. Alex, could you verify this please? The LED works fine on the production Zubax Orel 20, perhaps the open sourced design has a mistake in it, or the @taskx6004 has soldered it incorrectly indeed.

j3qq4hch, 2017-06-08:
I checked it again. Zubax Orel  and sapog reference have identical led connection. I guess, fab soldered it wrong. We have already seen this before

pavel-kirienko, 2017-06-08:
Thanks, Alex. Nothing unheard of indeed, PCB vendors have a thing with this type of LED.

Closed 2017-06-08.

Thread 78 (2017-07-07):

Pixhawk LED Module Chip?

tubeme, 2017-07-07:
Hello guys,

We are trying to design our own LED module for the Pixhawk controller. As far as we understand there is a chip on the board that recieves information from I2C bus then accordingly controls the led. Some sort of LED driver with I2C control.

I suppose there is firmware that is doing the math?

So we've had a LED module that we like but it uses a chip that is no longer available. It is out of production etc. It is Toshiba chip TSA62724.

So my question is there any other chip that can be used for the LED module to drive the leds from I2C?

Thank you in advance.

LorenzMeier, 2017-07-07:
Let me have a look. I would be happy to add support for a new model.

igalloway, 2017-08-05:
It's not clear what the overall goal is with this new "LED Module". I just thought i would mention a couple of parts, as a flexible options for driving both a few (RGB) and many LEDs:
Hopefully helpful?

[NExperia NPIC - Shift register based, cascade-able](https://www.nexperia.com/products/logic/family/NPIC/#/p=1,s=0,f=,c=,rpp=,fs=0,sc=,so=,es=)

[NXP Selector guide](http://www.nxp.com/products/interfaces/ic-bus-portfolio/ic-led-controllers:MC_48878#/&page=2)

[NXP I2C based - PCA9634](
http://www.nxp.com/products/interfaces/ic-bus-portfolio/ic-led-controllers/8-bit-fm-plus-i2c-bus-led-driver:PCA9634)

[NXP I2C based - PCA9551, Fast mode with Programmable blink rates](http://www.nxp.com/products/interfaces/ic-bus-portfolio/ic-led-controllers/8-bit-i2c-bus-led-driver-with-programmable-blink-rates:PCA9551)

tubeme, 2017-08-05:
Thanks a lot guys!! Appreciated @LorenzMeier @igalloway

tubeme, 2017-08-06:
@LorenzMeier @igalloway If we use one of these chips do we need a driver for it or it is in PX4 already?

igalloway, 2017-08-07:
Can you explain a bit more what you are trying to do?
I'm assuming this is either some kind of remote status indicator?

There are external SPI ports on most PX4 hardware.
There are software drivers for SPI communications
To actually control and illuminate the LED(s) in whichever way you want
would require some software written both to control the SPI device and then
control the LED(s) in the way you want.

On Sun, Aug 6, 2017 at 5:27 PM, Vasil Petrov <notifications@github.com>
wrote:

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

tubeme, 2017-09-21:
@igalloway We are going to use it for a Status Leds for the PX4. So probably we have to implement it ourselves because there is no chip that could be used right out of the box for now. The one's used are discontinued.

a146860, 2018-08-14:
What replacement

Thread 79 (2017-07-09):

The HMC5983 in FMUv3

zouboan, 2017-07-09:
I bought a pixhawk 2.1 from HEX recently，I
found that the PCB of FMUv3  i bought is different from https://github.com/PX4/Hardware/tree/master/FMUv3_REV_D
for example:the PCB of FMUv3 have a HMC5983,but what I bought was not included！

lumber3, 2018-04-10:
HMC5983 is closed product .replaced by new IC

pkocmoud, 2018-05-22:
The choice of components is determined by the manufacturer and device availability. You should contact the specific manufacturer if you need assistance on this.

Closed 2018-05-22.

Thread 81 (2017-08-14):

Problem in documentation for "Remote Control RSSI" documentation page

R-Ronald, 2017-08-14:
In the Analog input section of the Remote control RSSI page ([](https://pixhawk.org/users/rc_rssi)), there is an example of connecting a FRsky X8R to a Pixhawk. In the picture, a 3 pin RC servo cable is used between the receiver’s RSSI out and the Pixhawk SBUS in.

I don't have an X8R, but this is a dangerous practice for at least some FRsky receivers. If you connect all three pins for monitoring RSSI, the center conductor can carry power back to the Pixhawk. On my Pixhawk (admittedly a clone), this results in powering the servo rail thru the FRsky LR9 radio receiver.

In other words, even though the Pixhawk is not powering the servo rail, it does power the RCIN connector so that the RC receiver will be powered. And the SBUS port that monitors analog RSSI evidently does have its 5v pin connected to the servo rail power bus. Thus, the servo rail can inadvertently be powered via the RSSI monitoring cable.

On my maiden flight, I had over .9 volt of excursions on my Pixhawk VCC signal. I added capacitor filters for the second flight with some improvement, but did not solve the problem. I finally realized that the servo rail was being powered from the RSSI signal in addition to my UBEC and fixed the problem today.

Since your example picture shows all three conductors for this cable, I believe that you should warn users to make sure they are not inadvertently powering their servo rail thru this connection.

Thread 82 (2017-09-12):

help ! px4io not found error

mehrdadshiri, 2017-09-12:
hi every body
i was flying my pixhawk on a quad-copter for the first time and suddenly an alarm came off and and it landed.
so I connected the usb right after and now it says px4io not found in mission planer and the on the Qground control it says "cannot communicate"  . i have read on the net that some people suggest to start with the safety switch pressed for firmware restart and it didn't help at all and the switch is not blinking anymore.
has anyone had a same experience before or have any suggestions to fix this ?

hamididari, 2018-03-17:
hi
can you check the px4io micro is health or not (connect to px4io via st link and read memory)

pkocmoud, 2018-05-22:
@mehrdadshiri - Please seek assistance on this issue from your hardware supplier or the flightstack software's discussion board. http://discuss.px4.io/ for PX4.

Closed 2018-05-22.

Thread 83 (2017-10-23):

the boom of  Pixhawk 2

caiganggang, 2017-10-23:
Would you like to tell me the all material list.Especially the connectors model,where could i buy  it ? Think you!

proficnc, 2017-10-23:
You can purchase Pixhawk 2 from any ProfiCNC reseller

kd0aij, 2017-10-23:
I think he meant BOM

caiganggang, 2017-10-23:
yes .I'd like to know the boom of  connectors and  where to buy it

Closed 2017-10-23.

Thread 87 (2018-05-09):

4 crashes without understanding the correct cause

samiresmaili, 2018-05-09:
Hello
I have four flights that have led to a fall. One of them is in altitude mode, for which an alert has been recorded at the moment of imbalance and three of them are in mission mode, for which there is no error for them at the moment of imbalance. To understand the cause of the crashes, Please help me.
Altitude flying number 1: there is initially a registered warning shown in the image below and an error at the moment of crash. What should you do to fix this error?
 
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

Flight 2: a warning was initially recorded, but nothing has been recorded at the moment of the crash. Full information on the log
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
 
flight 3: no warning or error has been given at the moment of crash. Full information on the log.
 
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

flight 4: no warning or error has been given at the moment of crash. Full information on the log.
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

flight 1: https://review.px4.io/plot_app?log=0e0f0aaf-5c42-480e-9d62-e08dfb70a891
flight 2: https://review.px4.io/plot_app?log=9194034e-8b81-4026-a421-0a1ca49f21e7
flight 3: https://review.px4.io/plot_app?log=4b227795-7069-4809-a804-cadf567e3a32
flight 4: https://review.px4.io/plot_app?log=06c0982d-6c37-4d9a-89d6-1692d3ab2e63

pkocmoud, 2018-05-22:
@samiresmaili - Please seek assistance on this issue from your hardware supplier or the flightstack software's discussion board. http://discuss.px4.io/ for PX4.

Closed 2018-05-22.

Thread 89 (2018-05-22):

Pixhawk 4 (FMUv5)

astekachev, 2018-05-22:
Hi!
I have a couple of questions.
Will Pixhawk 4 schematics and PCB Project be available for public access in the near future?
Or Pixhawk 4 is commercial project and the project schematics with PCB Project will be closed?
Thank you!

pkocmoud, 2018-05-22:
As I understand it, FMUv4 and FMUv5 designers are only required to release a microcontroller reference pinouts for software compatibility. So you should not expect to find specific schematics or board design files unless the original designer chooses to release them.

Closed 2018-05-22.

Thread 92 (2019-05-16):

Can't find Schematics and Layout of FMUv5

gcarmix, 2019-05-16:
Hi, I can't find schematics and layout of FMUv5 is it no more open hardware??

pkocmoud, 2019-05-16:
@gcarmix - The FMUv5 standard is only provided as an list of pin assignments and their functional descriptions as a reference for software compatibility found here:

[https://github.com/PX4/Hardware/tree/master/FMUv5](https://github.com/PX4/Hardware/tree/master/FMUv5 )

The circuit design is up to the individual designers and as it is not one of my designs I don't have any additional information.

Closed 2019-05-16.

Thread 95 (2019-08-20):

How to connect pixhawk 2.4.8 to Nvidia Jetson Nano?

atmadeep, 2019-08-20:
Hi, I'm working on making a semi autonomous drone using vision based methods. Has anyone tried connecting a pixhawk 2.4.8 with jetson Nano? Any help would be appreciated

dogmaphobic, 2019-08-20:
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

The UART pins are separate for easy reach.

atmadeep, 2019-08-20:
Have you tested this over ROS? Can you get the messages in mavros?

dogmaphobic, 2019-08-20:
Yes, there isn't really any difference than running mavros on an RPI or an Intel NUC (running a Debian Linux).

atmadeep, 2019-08-20:
Thank you very much.

atmadeep, 2019-12-02:
New problem here, Every time I connect jetson nano to pixhawk, it turns off and won't start again until disconnected. I'm not connecting the red/power cable.
What can be the problem now?

pkocmoud, 2019-12-02:
@atmadeep This is really not a place for usage assistance. You would have better luck in one of the discuss forums.

Depending on the flight software you are using you might try:

PX4: https://discuss.px4.io/
Ardupilot: https://discuss.ardupilot.org/

proficnc, 2019-12-02:
Make sure your voltage levels are correct on your io

busradurak, 2020-06-19:
> New problem here, Every time I connect jetson nano to pixhawk, it turns off and won't start again until disconnected. I'm not connecting the red/power cable.
> What can be the problem now?
Try to give power only the nano if you connect to power both of them, some problem might be occured.

oguzhanonder38, 2021-07-27:
> > New problem here, Every time I connect jetson nano to pixhawk, it turns off and won't start again until disconnected. I'm not connecting the red/power cable.
> > What can be the problem now?
> > Try to give power only the nano if you connect to power both of them, some problem might be occured.

Hello busra have you solved connection problem? If you solved the problem, please connect to me. Thx. : *

reinzler, 2023-06-05:
Hi, guys,  I usually have same problem, if Pixhawk had been connected to Jetson Nano before I powered on the Nano, Nano cant detect Pixhawk until I physically disconnect/ connect MicroUSB cable, Did someone find an answer?

hamishwillee, 2023-06-05:
Not the best place for this question - https://github.com/pixhawk/Hardware/issues/95#issuecomment-560539815

But if you find an answer cross post.

Closed 2023-06-05.

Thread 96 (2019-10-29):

Accelerometer calibration fail

RandomHacksYoutube, 2019-10-29:
Hi, I have an PX4FMUv2.4, when I try to calibrate the accelerometer in mission planner it asks me to level the pixhawk, position left, and right and then it fails, every single time, no matter how still I am during this proccess. I already replaced MPU6000, L3GD20 and LSM303D but it made no difference. I don't even know how to debug this issue, can somebody shed some light on this? Is there a way to know which of these 3 ICs is causing the problem or if it is something else?

pkocmoud, 2019-10-29:
Hello @RandomHacksYoutube , this GitHub project issue section is more suited to fundamental design flaws. You will want to head over to https://discuss.ardupilot.org/ for assistance with this sort of issue.

RandomHacksYoutube, 2019-10-29:
I believe this is a hardware issue so I thought this would be the place, but I will head over there then. Thanks.

pkocmoud, 2019-10-29:
I understand but the software project's support could help you understand which sensor is causing your trouble by reviewing your logs. The Pixhawk design is fundamentally sound and it seems most likely the issue you are experiencing is specific to your board.

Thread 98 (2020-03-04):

Radio Telemetry through Companion Computer

darshanz, 2020-03-04:
Is there any way to use radio telemetry through companion computer which is already communicating with Pixhawk and the serial port is being used by companion computer for reading other sensor data?
The companion computer is connected via UART with Jetson/TX2. Currently I have Radio connected to Pixhawk but I am trying to use gcs through companion computer having single connection with FC as all the ports on FC are used up by other sensors.
Thanks.

devbharat, 2020-03-04:
You can start mavlink instance communicating with companion computer with 'forwarding' switched on.

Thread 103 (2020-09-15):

Use Pixhawk with EMAX BLHeli Series ESCs

9friday, 2020-09-15:
This is not an issue, but a preemptive query.

Are the EMAX ESCs compatible with the Pixhawk?
This [link](https://ardupilot.org/copter/docs/connect-escs-and-motors.html) from the Ardupilot website still states the Pxhawk has a problem with EMAX ESCs, although this [issue](https://github.com/ArduPilot/ardupilot/issues/2094) over at the Ardupilot repo is closed and someone has answered that the issue with EMAX SimonK ESCs has been resolved.

Has the issue only been resolved for specific EMAX ESCs or all of them?

mituritsyn, 2022-08-22:
I've faced similar issue with another esc. This is due to low resistance on esc signal pin lead to PWM amplitude lowering so ESC couldn't recognise it

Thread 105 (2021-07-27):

Pixhawk 2.4.8 and Jetson Nano Connection

oguzhanonder38, 2021-07-27:
We have a problem with connecting pixhawk to Jetson Nano. Is there anyone who connects two of them before? There is much information about pixhawk and raspberry. Is it similar? We are waiting for your help. Thx. : *

ahmetakifsaglam, 2021-07-27:
What is your Ubuntu version?

oguzhanonder38, 2021-07-27:
Ubuntu version is 20.04.2

proficnc, 2021-07-27:
The Nano has some timing issues that can cause difficulties, best to ask on the Ardupilot forums or PX4 forums (depending on what you are using)

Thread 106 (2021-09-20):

Pixhawk 4 - GPS, Safety switch and buzzer connection problems problem

FeCLN, 2021-09-20:
Hello, I am from Skyrats, a Brazilian autonomous drone team. Recently we bought a Pixhawk 4 with the intention of using it with some other components in the GPS port, along with the GPS of course. These components are: a normal safety switch, a buzzer, and a SE100 GPS (All of them tested in a Pixhawk 1 and working normally). After making some wiring connections; all of them accordingly to each datasheet and pinout, we tried to use it in a Pixhawk 4, but unfortunately we didn't have good results. The safety switch didn't work, the LED didn't light up, and checking with a voltmeter we didn't even get any signal from these ports. The buzzer makes a sound, but it's completely inaudible. And the worst part is, the GPS didn't work, in QGroundControl we receive only a "0 satellites found with 0 signal strength". Has anyone had this problem? What can we do?

hamishwillee, 2021-09-21:
Hi @FeCLN,
I'm going to close this because it is not a good place to ask this question. This is an area for the Pixhawk design, so you'd post an issue here if you had an issue with the Pixhawk specification, not with specific hardware.

The best place for this question would be the PX4 discuss server or Slack. That way you will get many more people seeing your question: See http://docs.px4.io/master/en/#getting-help

Closed 2021-09-21.

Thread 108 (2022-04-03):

Why new pixhawk hardware use USB3.0?

South-River, 2022-04-03:
Hi!
I used pixhawk for two years. I noticed that new versions of pixhawk use USB3.0 for communication. But as far as I know, there's no large data sent and received by pixhawk. Although IMU needs high frequency, maybe IIC and SPI can do this job.
So I'm wondering why new pixhawk use USB3.0?
Thanks!

davids5, 2022-04-03:
On the new V5X, V6X , It is a type C connector with USB 2.0 FS signaling. HS is not used.

Closed 2022-04-03.

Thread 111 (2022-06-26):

FMU 5x/6x Baseboard

seankovacs, 2022-06-26:
Hello,
I'm attempting to create a custom carrier/base board for the FMUv5x/6x module. Reviewing the Autopilot Standard which HolyBro seems to be the only one support (!?), I initially was under the impression that the base/carrier board was simply a companion that hosted external ports that feed the main module. After further review, it seems the baseboard hosts a IO MCU and EEPROM (among other simple circuits).
Few questions if you don't mind:

- How come there isn't any documentation on the baseboard IO MCU pinouts? How do the pins map to the Main MCU?
- Since there are existing controllers that don't have an IO MCU, I'm assuming you can create a baseboard without it?
- I see that there is a EEPROM on the baseboard? What/who programs it?

davids5, 2022-07-06:
> Hello, I'm attempting to create a custom carrier/base board for the FMUv5x/6x module. Reviewing the Autopilot Standard which HolyBro seems to be the only one support (!?), I initially was under the impression that the base/carrier board was simply a companion that hosted external ports that feed the main module. After further review, it seems the baseboard hosts a IO MCU and EEPROM (among other simple circuits). Few questions if you don't mind:
>
> * How come there isn't any documentation on the baseboard IO MCU pinouts? How do the pins map to the Main MCU?

The IO is optional. But there has not been a board done for the VxX that did not use it.

This is a serial connection. Referring to  https://github.com/pixhawk/Hardware/blob/master/FMUv2/PX4FMUv2.4.5.pdf Sheet 8
will get you the wiring. @mrpollo is there more docs you can share with  @seankovacs?

> * Since there are existing controllers that don't have an IO MCU, I'm assuming you can create a baseboard without it?

Yes.

> * I see that there is a EEPROM on the baseboard? What/who programs it?

Ethernet configuration and device manifest

See https://github.com/PX4/PX4-Autopilot/blob/main/boards/px4/fmu-v5x/src/mtd.cpp#L41 and
https://github.com/PX4/PX4-Autopilot/blob/main/boards/px4/fmu-v5x/src/mtd.cpp#L69-L82

The application `netman` manages the Ethernet configuration.

Device manifest will be used in the future for a "device tree" like description of the devices connected. It is a versioned data struct and currently in used to expand the HW VER ID when the R1/R2 is set to code point 7. It is programed by the MFG when used.

seankovacs, 2022-07-06:
Thanks for your response @davids5 . So it sounds like the EEPROM is optional as well? Especially if the need for ethernet is not needed?

davids5, 2022-07-06:
If you are going to have a custom board and build of the firmware you can do what ever you like. But it will not be compatible with the exiting PAB V5X and V6X  FMUM's built by the current manufactures and will not be PX4 VxX compatible.

alekh1stzoom, 2023-01-27:
Does anyone you have the schematic for the FMU v6x?

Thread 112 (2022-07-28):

Several question about schematic of fmu 2 and 3

Trinity030, 2022-07-28:
Why Fmu mcu communicate with Io mcu series 220 ohm ?
for impedance matching ??

davids5, 2022-07-28:
In the old days, the IO could land a FW (not really feasible with MC) with Fail Safe manual RC control if the FMU died.

So the 22R was for Isolation to limit the current incase of a catastrophic failure on the FMU SoC.

In a recent PR the IO was lobotomized so the value add of the isolation is almost nothing.

davids5, 2022-07-29:
Firmware is here https://github.com/PX4/PX4-Autopilot or builds are under actions i.e.  https://github.com/PX4/PX4-Autopilot/actions/runs/2753822626

Schematics are here https://github.com/pixhawk/Hardware

proficnc, 2022-07-30:
This is still critical, in a PX4 FMzU power failure, the IO may possibly still be powered

Also, though some forget... Pixhawk "Hardware" was an ARDUPILOT AND PX4 effort, and Ardupilot still has RC pass through which is a critical safety feature used by many many.

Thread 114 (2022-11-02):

Lost power on current main power brick causing the avionic reboot

hitagisol, 2022-11-02:
I notice that in the case when multiple power bricks present, if the current main power source failed the avionic will reboot.
Here is the test I've made on Pixhawk 5X:
 - Hardware setup: Connect Power 1, Power 2, USB as power source, Power 1 and Power 2 come from the Holybro PM03D module and the USB comes from my laptop.
 - Test procedure:
    1. Remove the connector from Power 1, while the Power 2 and USB remains connected, the avionic goes into the reboot routine.
    2. Remove the connector from Power 2 while the Power 1 and USB remains connected, the avionic keeps working without reboot.
    3. Remove the connector from Power 1, trigger the avionic goes into reboot. After the reboot, remove the connector from Power 2, the avionic reboots again.
Right now I'm assuming this is caused by the path switch handled by the LTC4417 controller, but I have no idea what test I can perform to prove that.

hitagisol, 2022-11-04:
@LorenzMeier I'm sorry for the manually ping but since this repo is not so popular I don't know if there is someone taking issues here periodically.

davids5, 2022-11-04:
@hitagisol Have you verified this on more than one FMU?

hitagisol, 2022-11-05:
>

@davids5 I have the same results on two different Pixhawk 5x. On the Pixhawk 4 board I do not have this issue. Currently I only have these three board in my hand.

vincentpoont2, 2022-11-07:
@hitagisol May I ask where you purchase this unit from? I have also sent you an email. Please check.

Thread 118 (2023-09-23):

Inquiry: Dimensions information

Husseinhajjsleiman, 2023-09-23:
Hello,

Hope you're doing well. I hope that I am not asking in the wrong place but I searched a lot without any success.

I am looking for internal dimensions for the Pixhawk 6x. Specifically, I am interested in knowing the vertical and/or horizontal offsets of the Inertial Measurement Unit (IMU) with respect to the center point.

Your assistance in providing this information would be greatly appreciated. Should you require any further details or clarification, please do not hesitate to reach out.

Thank you in advance for your time and consideration.

davids5, 2023-09-24:
You can refer to https://github.com/pixhawk/Pixhawk-Standards/tree/master for X,Y and positions of the FMUM.

But since many vendors can implement the design, the isolation method used for the IMU PCBA can very greatly and so can the vertical dimension.

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

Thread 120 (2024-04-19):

Pixhawk board is short

asadmehmoodchaudhary, 2024-04-19:
I have a pixhawk2.4.8. Few days ago during testing i was trying to connect my pixhawk with Pi 4 and during the connection I accidently touch one of the telemetry output wire with the +12v. after that my px4 is short i disconnect it within 5 sec. but after that when i reconnect it few of the led of right side didn't blinks and also my px4 is not connected to the PC so i cant use it with ardupiolt. i open the pcb board and after a basic checkup i noticed that LG33 voltage regulator is over heated so i replace it with a new one but still my px4 is not working. can any one solve this issue or tell me the who can solve it. this can help me a lot. please guide

proficnc, 2024-04-19:
Best raise this with your pcb manufacturer, this is not a support forum

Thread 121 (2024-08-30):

I need help

Zawne, 2024-08-30:
I have a Dell Latitude E6540 Laptop. Currently it is reporting "No Bootable Devices Found" but the system BIOS still recognizes the 128gb SSD. This happened to me after I was in the process of reinstalling Windows and an error occurred after that the system no longer detected the hard drive. I need your help. Thanks!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

Closed 2024-09-01.

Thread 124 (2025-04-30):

Cannot connect to Both USB port(type C and JST) at once

NabinBhandari1, 2025-04-30:
I am using pixhawk 6X. I want to connect pixhawk to companion computer Rpi 5, and Laptop running Ubuntu for HITL test. problem is that i cannot connect both at once. How can I solve this problem.

davids5, 2025-04-30:
The connectors are wired in parallel. A user can only use one or the other at a time.

Closed 2025-04-30.

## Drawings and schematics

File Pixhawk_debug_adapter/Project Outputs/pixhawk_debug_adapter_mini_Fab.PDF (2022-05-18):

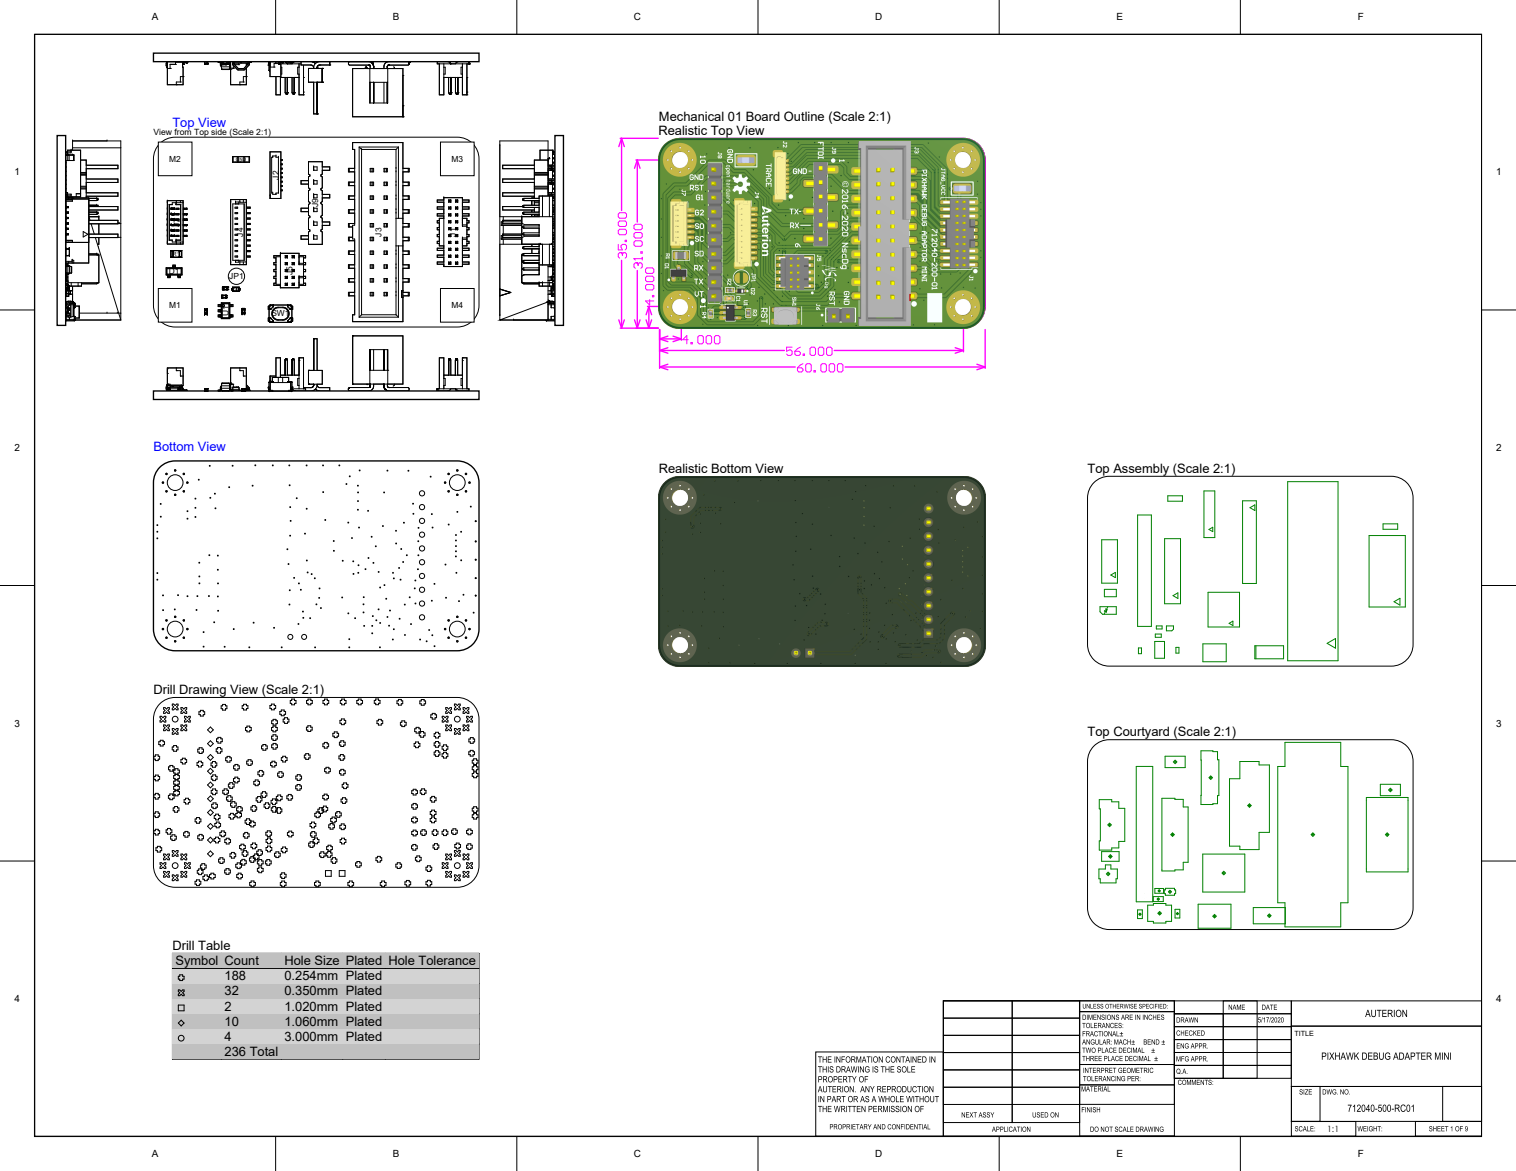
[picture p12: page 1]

Mechanical 01 Board Outline (Scale 2:1)
Realistic Top View

Top View
View from Top side (Scale 2:1)

Drill Drawing View (Scale 2:1)

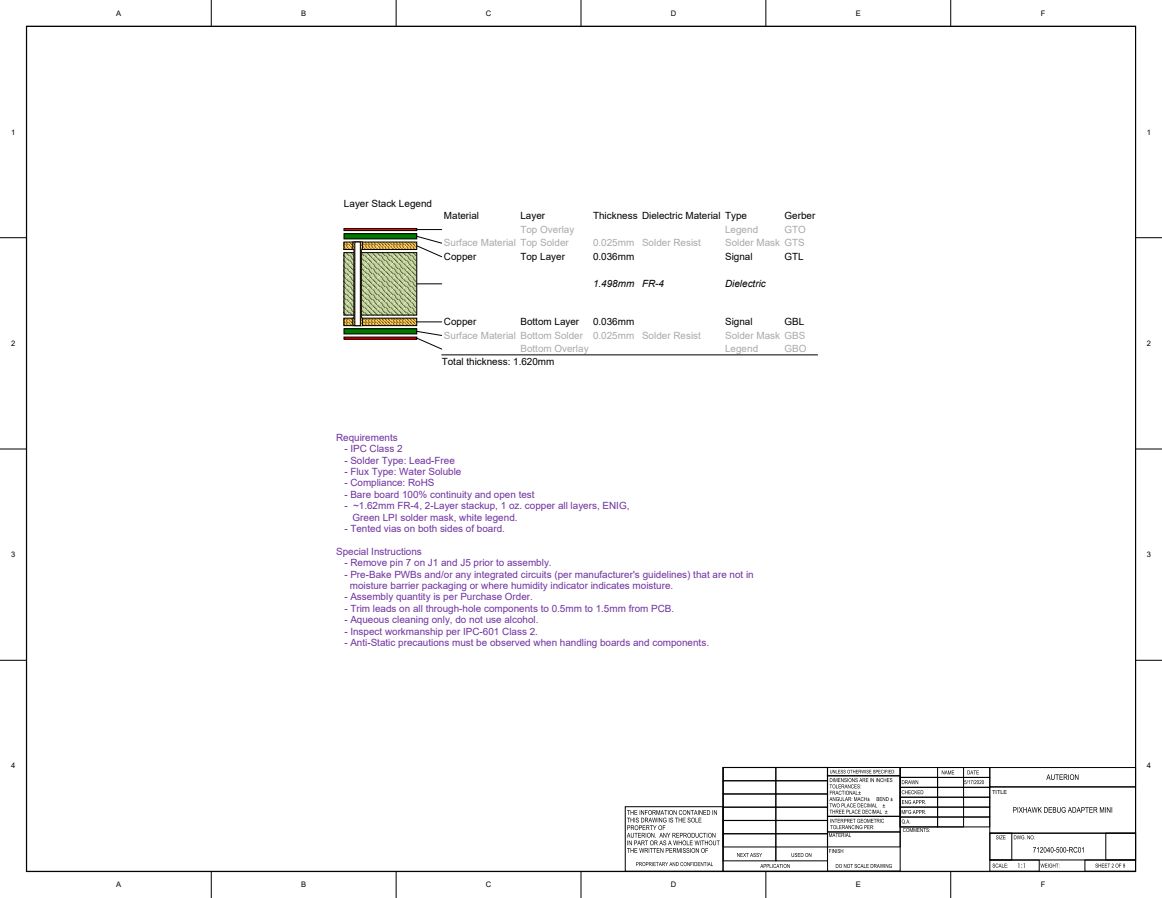
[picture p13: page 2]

Requirements
- IPC Class 2
- Solder Type: Lead-Free
- Flux Type: Water Soluble
- Compliance: RoHS
- Bare board 100% continuity and open test
- ~1.62mm FR-4, 2-Layer stackup, 1 oz. copper all layers, ENIG,
Green LPI solder mask, white legend.
- Tented vias on both sides of board.

Special Instructions
- Remove pin 7 on J1 and J5 prior to assembly.
- Pre-Bake PWBs and/or any integrated circuits (per manufacturer's guidelines) that are not in
moisture barrier packaging or where humidity indicator indicates moisture.
- Assembly quantity is per Purchase Order.
- Trim leads on all through-hole components to 0.5mm to 1.5mm from PCB.
- Aqueous cleaning only, do not use alcohol.
- Inspect workmanship per IPC-601 Class 2.
- Anti-Static precautions must be observed when handling boards and components.

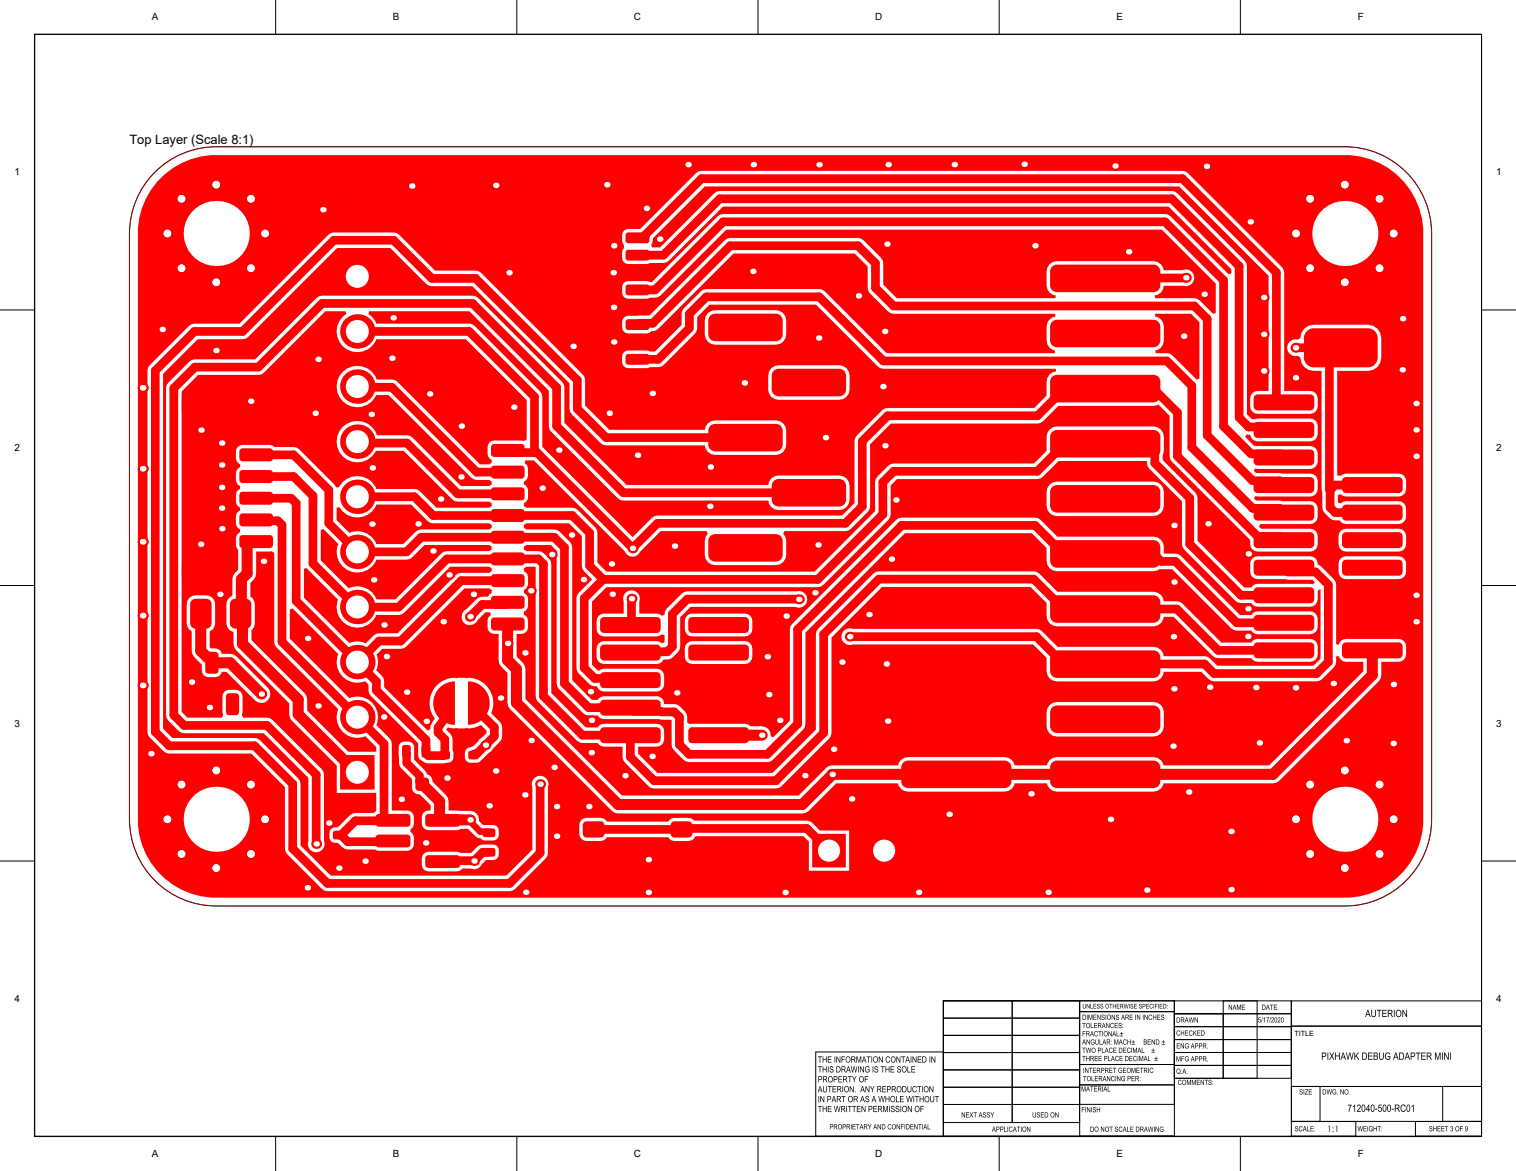
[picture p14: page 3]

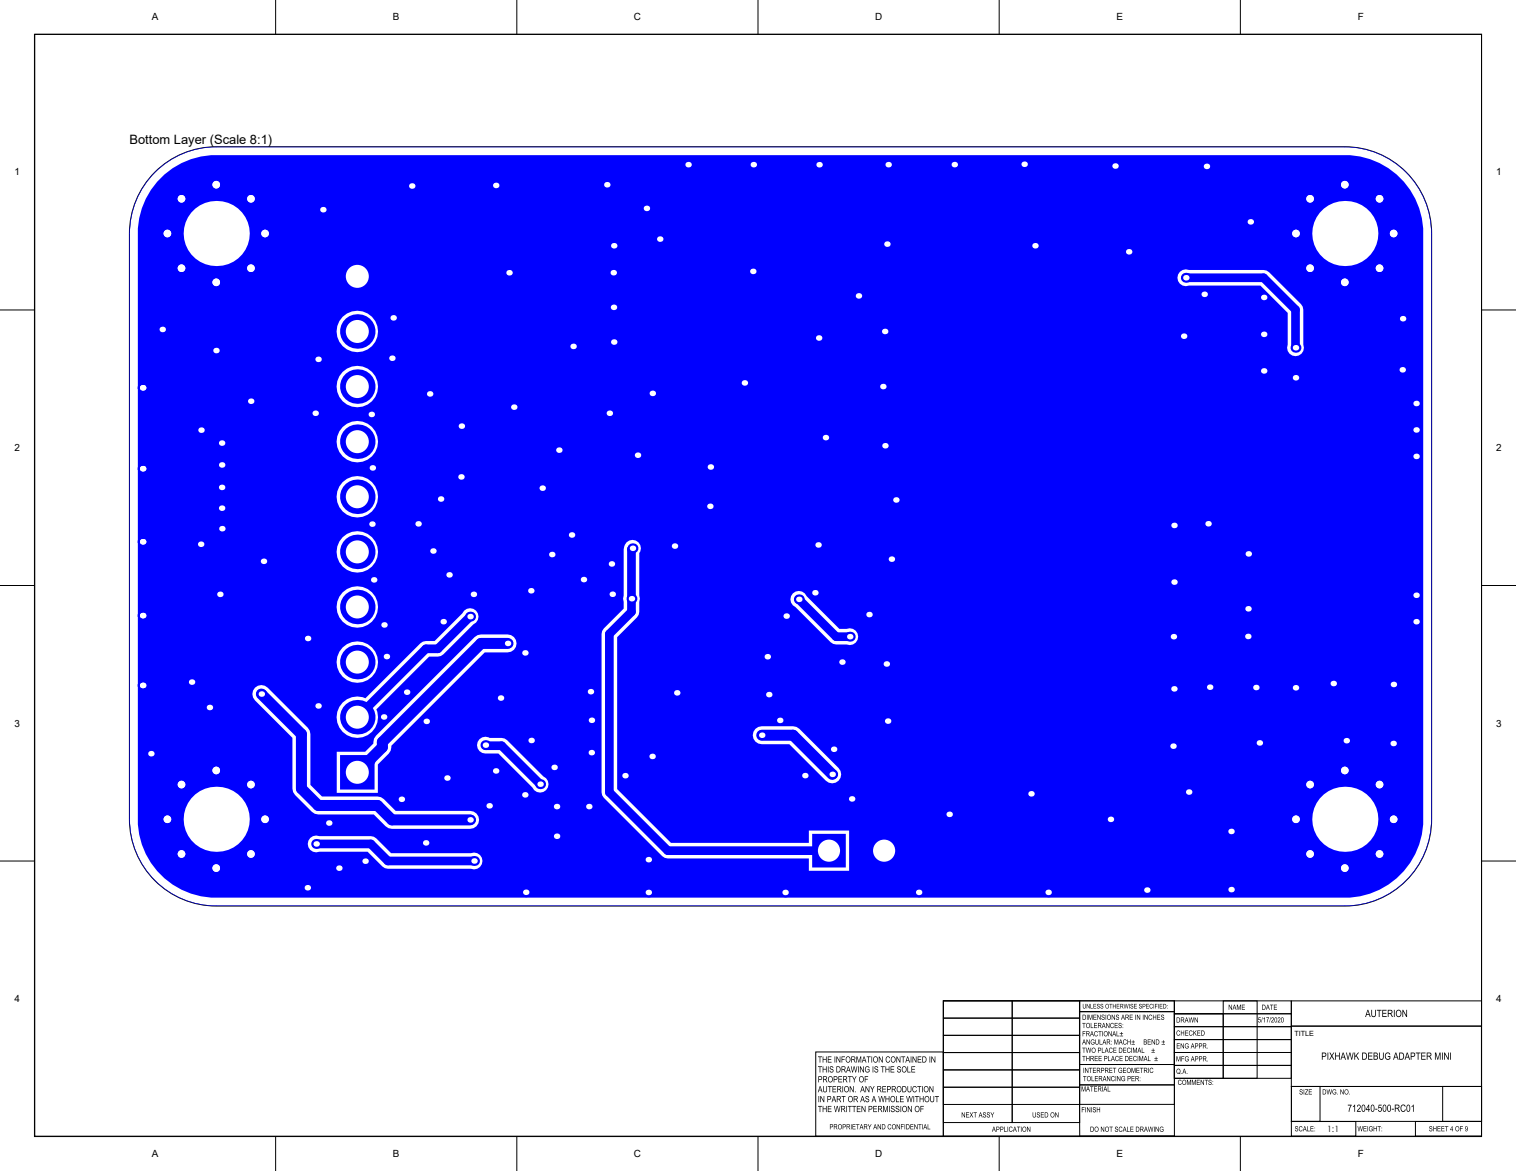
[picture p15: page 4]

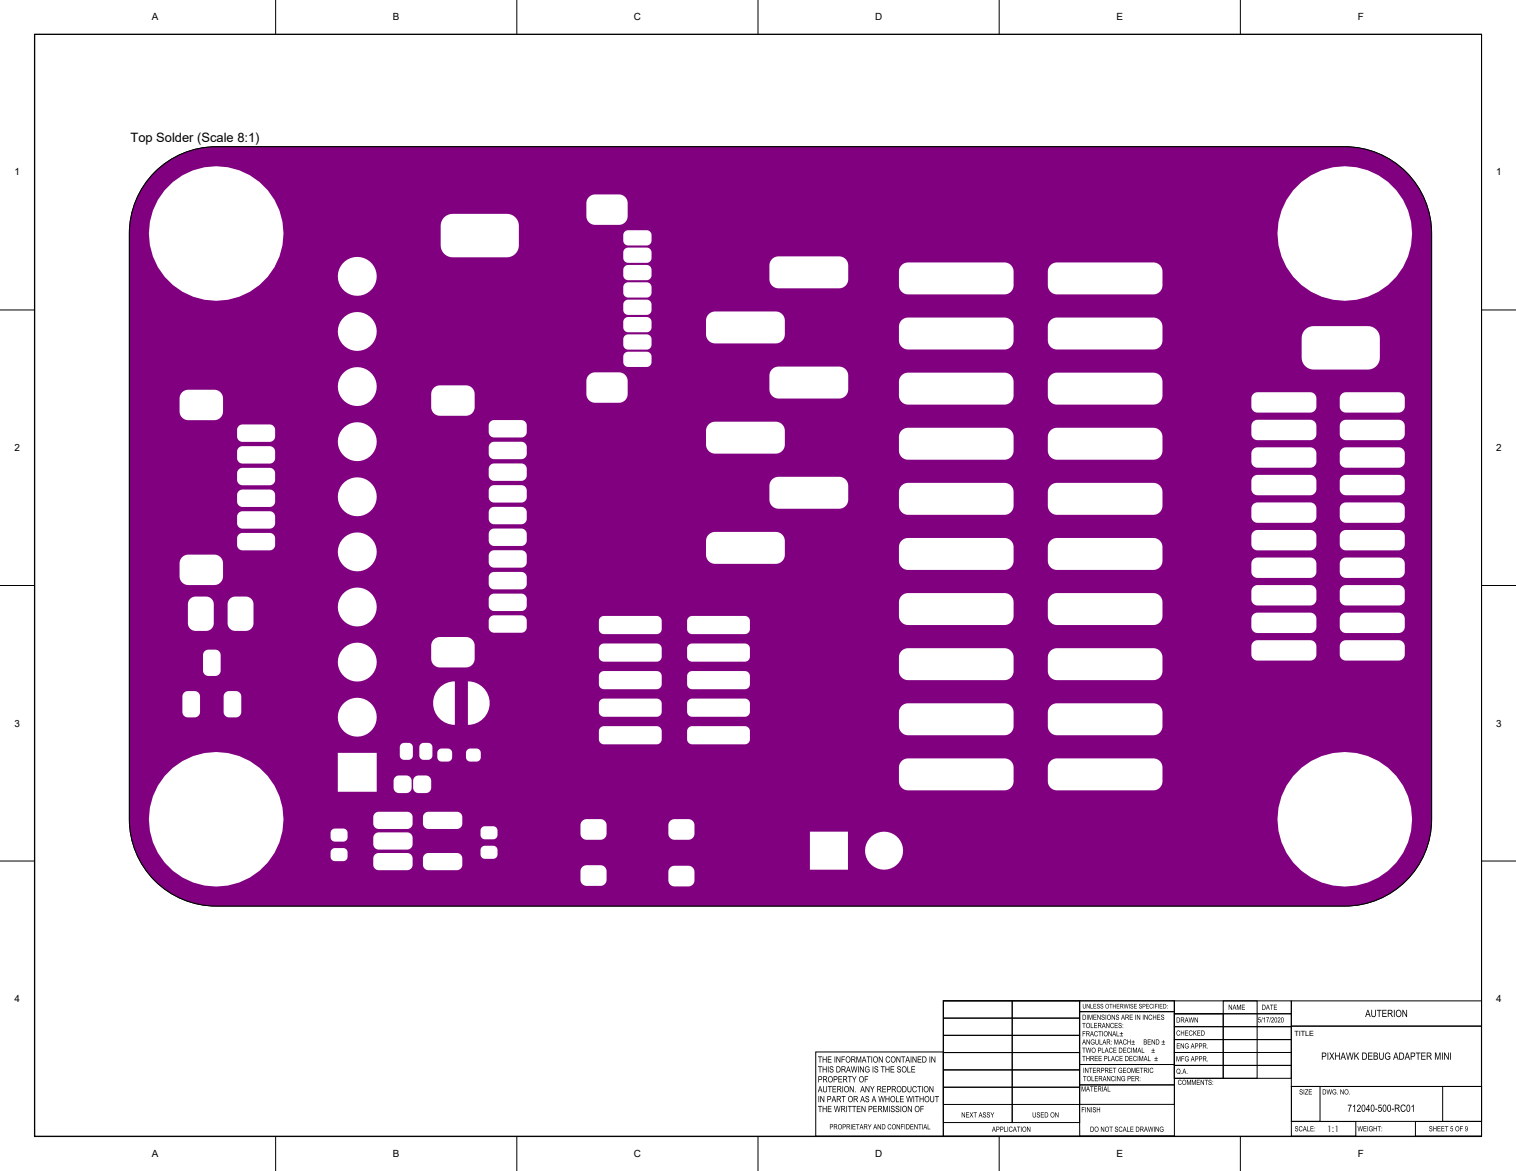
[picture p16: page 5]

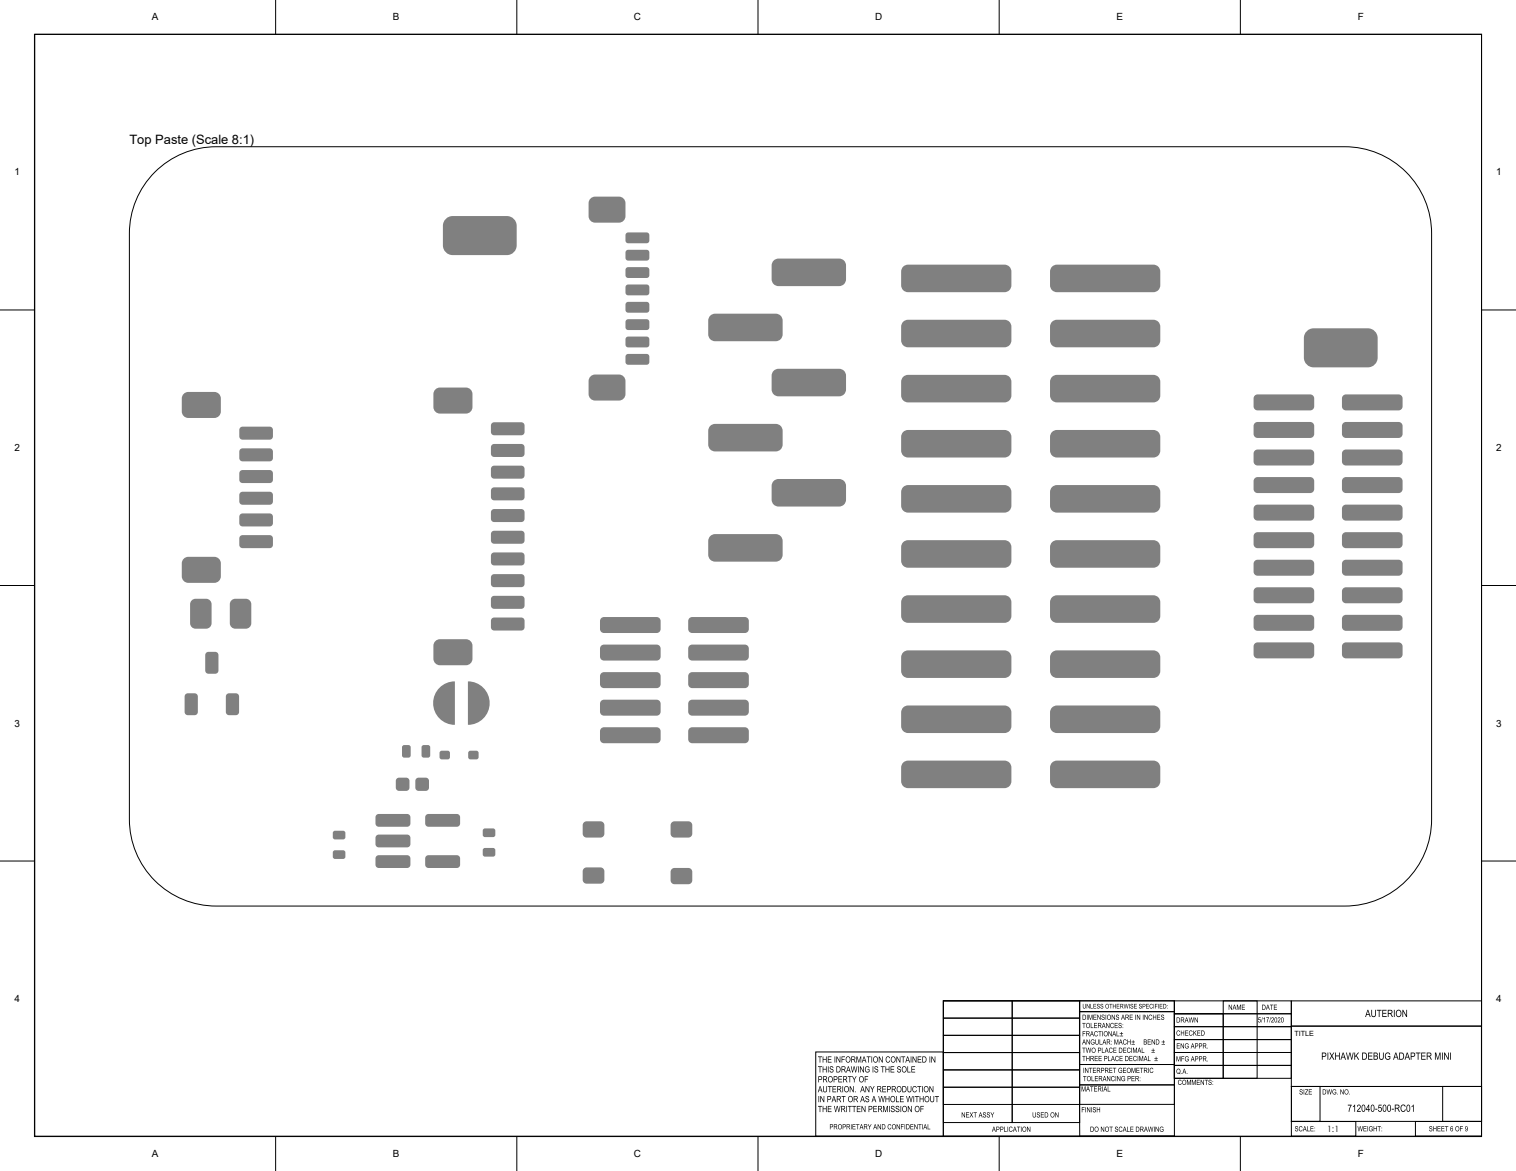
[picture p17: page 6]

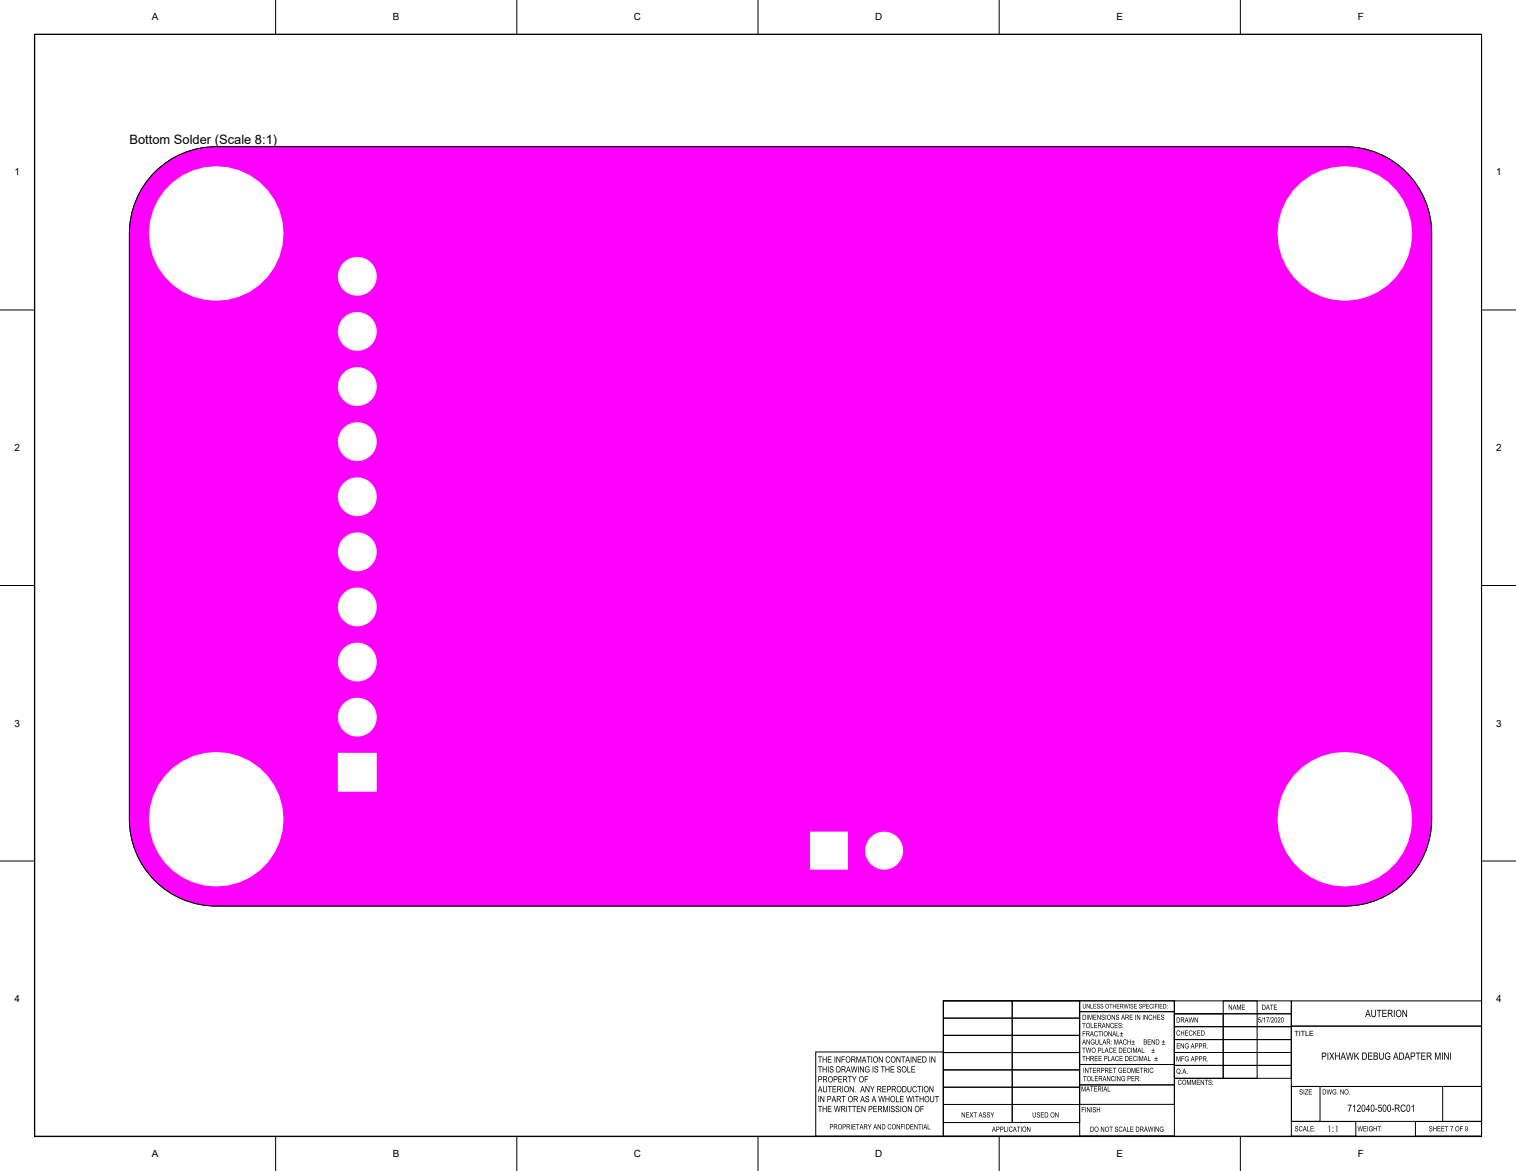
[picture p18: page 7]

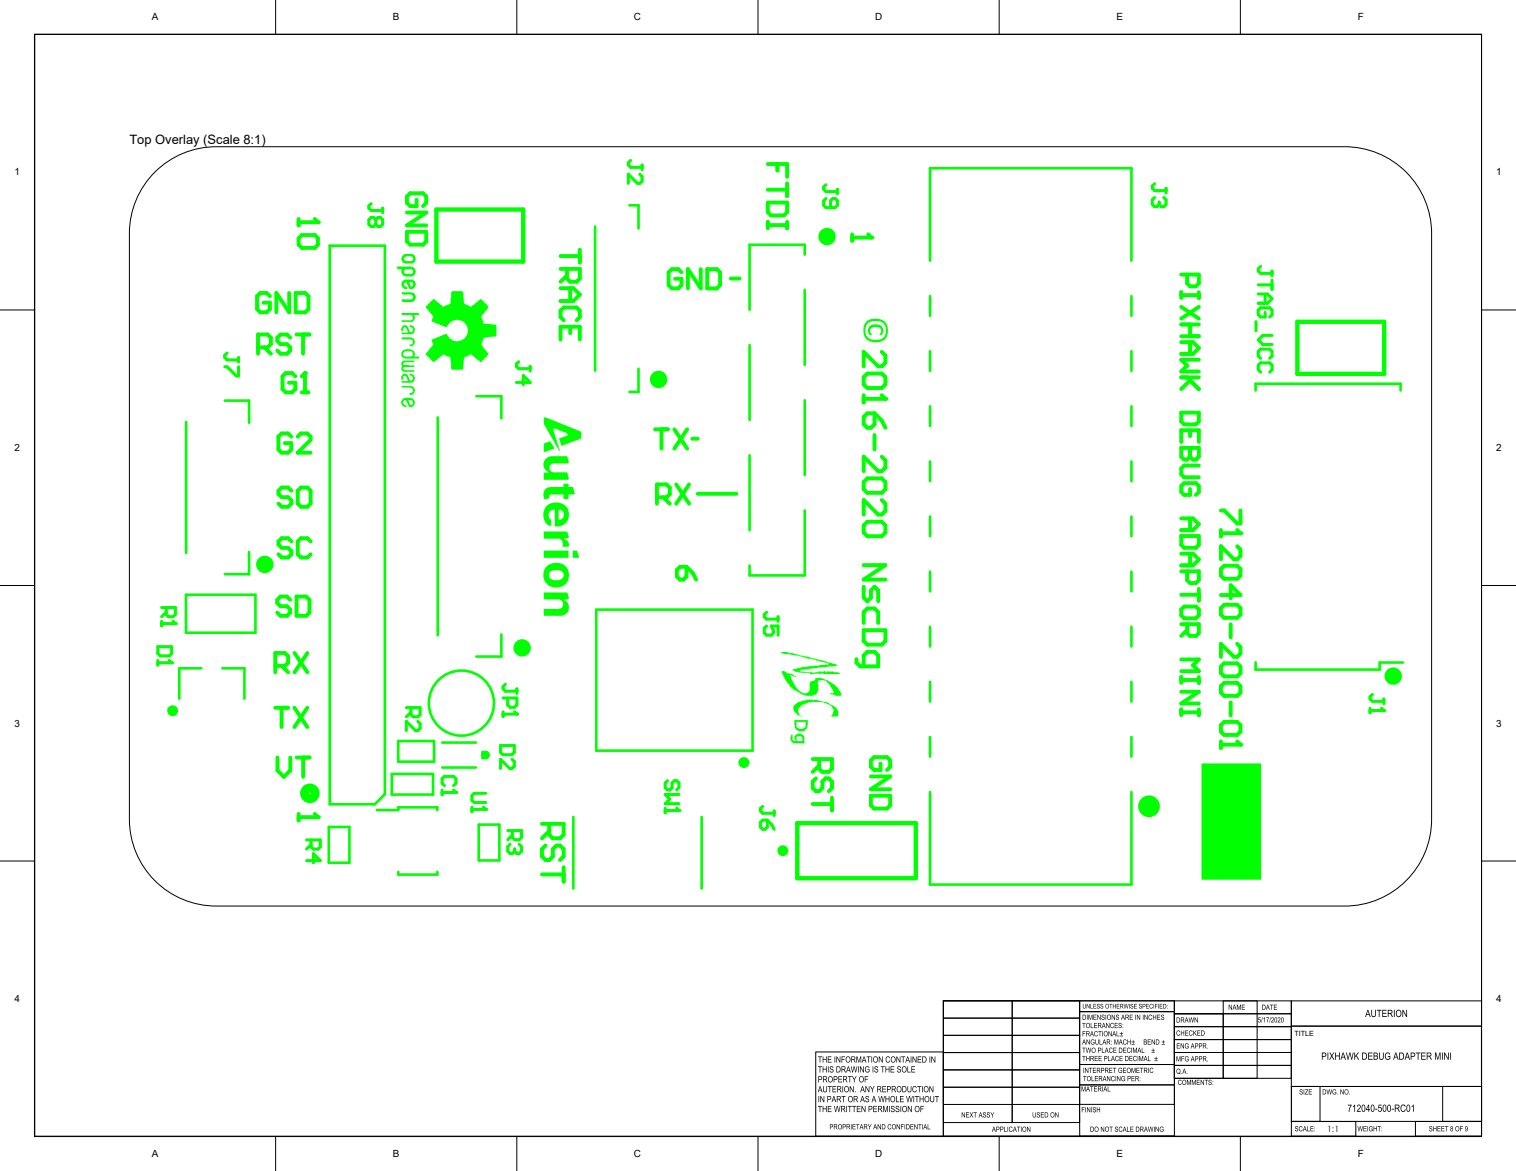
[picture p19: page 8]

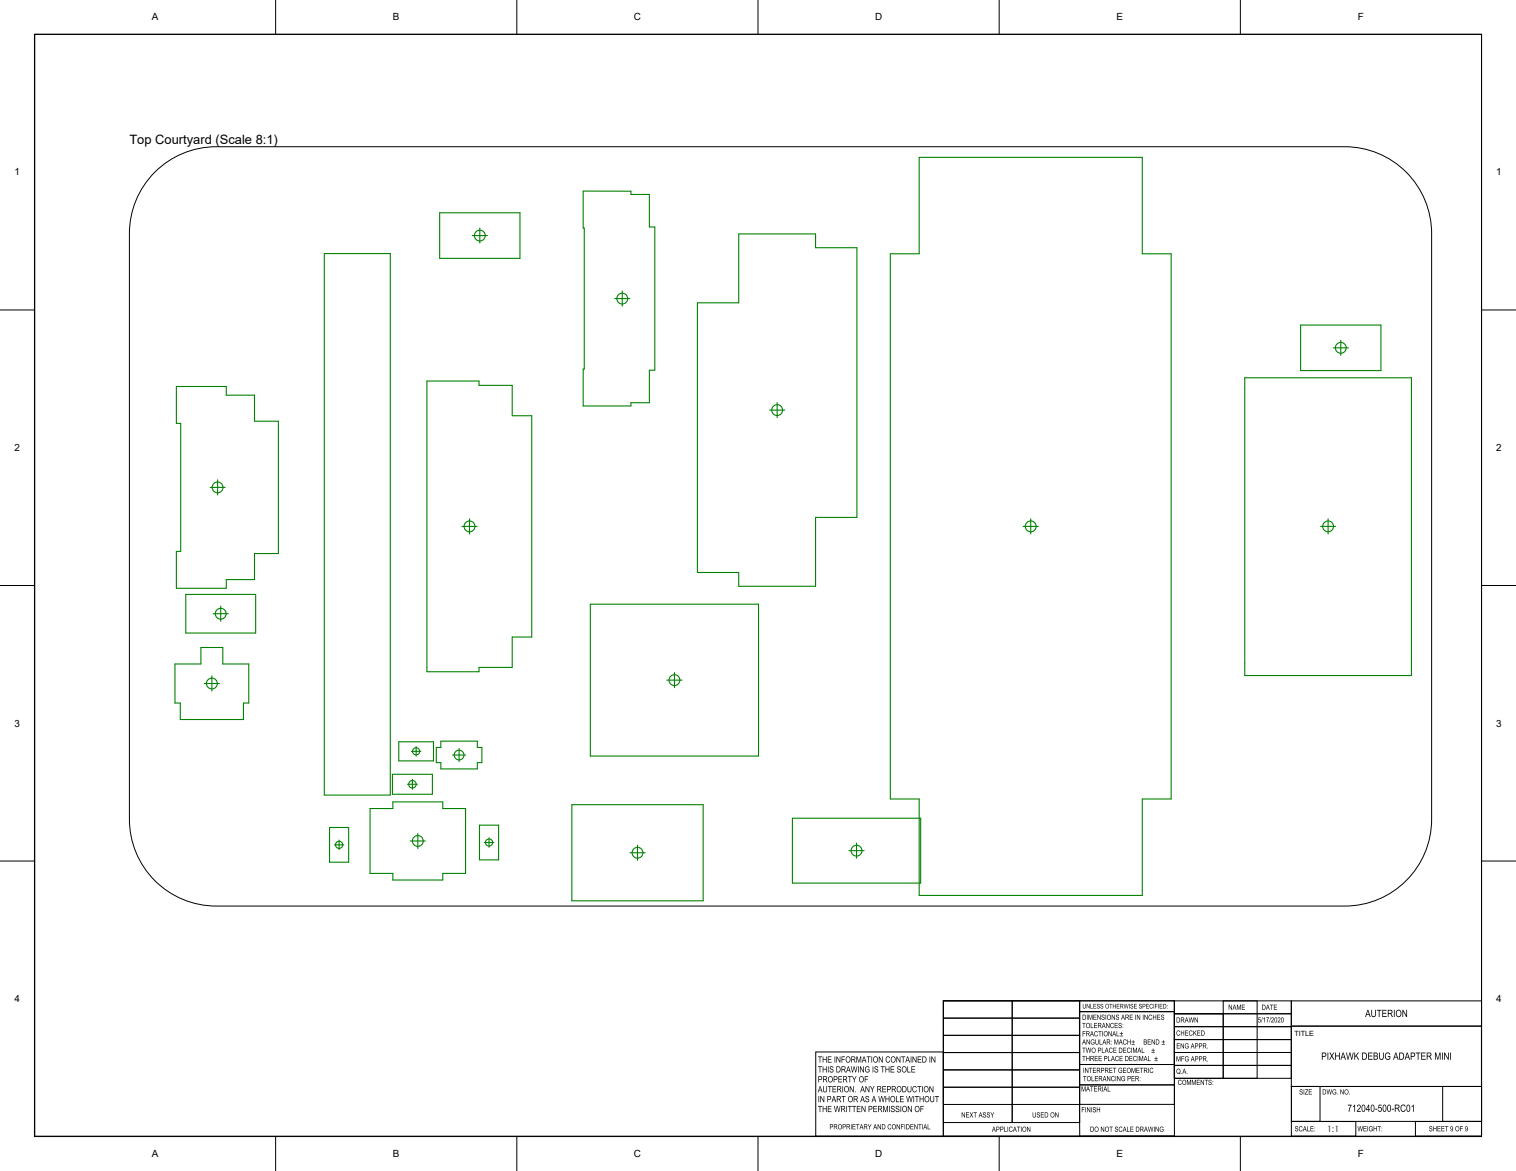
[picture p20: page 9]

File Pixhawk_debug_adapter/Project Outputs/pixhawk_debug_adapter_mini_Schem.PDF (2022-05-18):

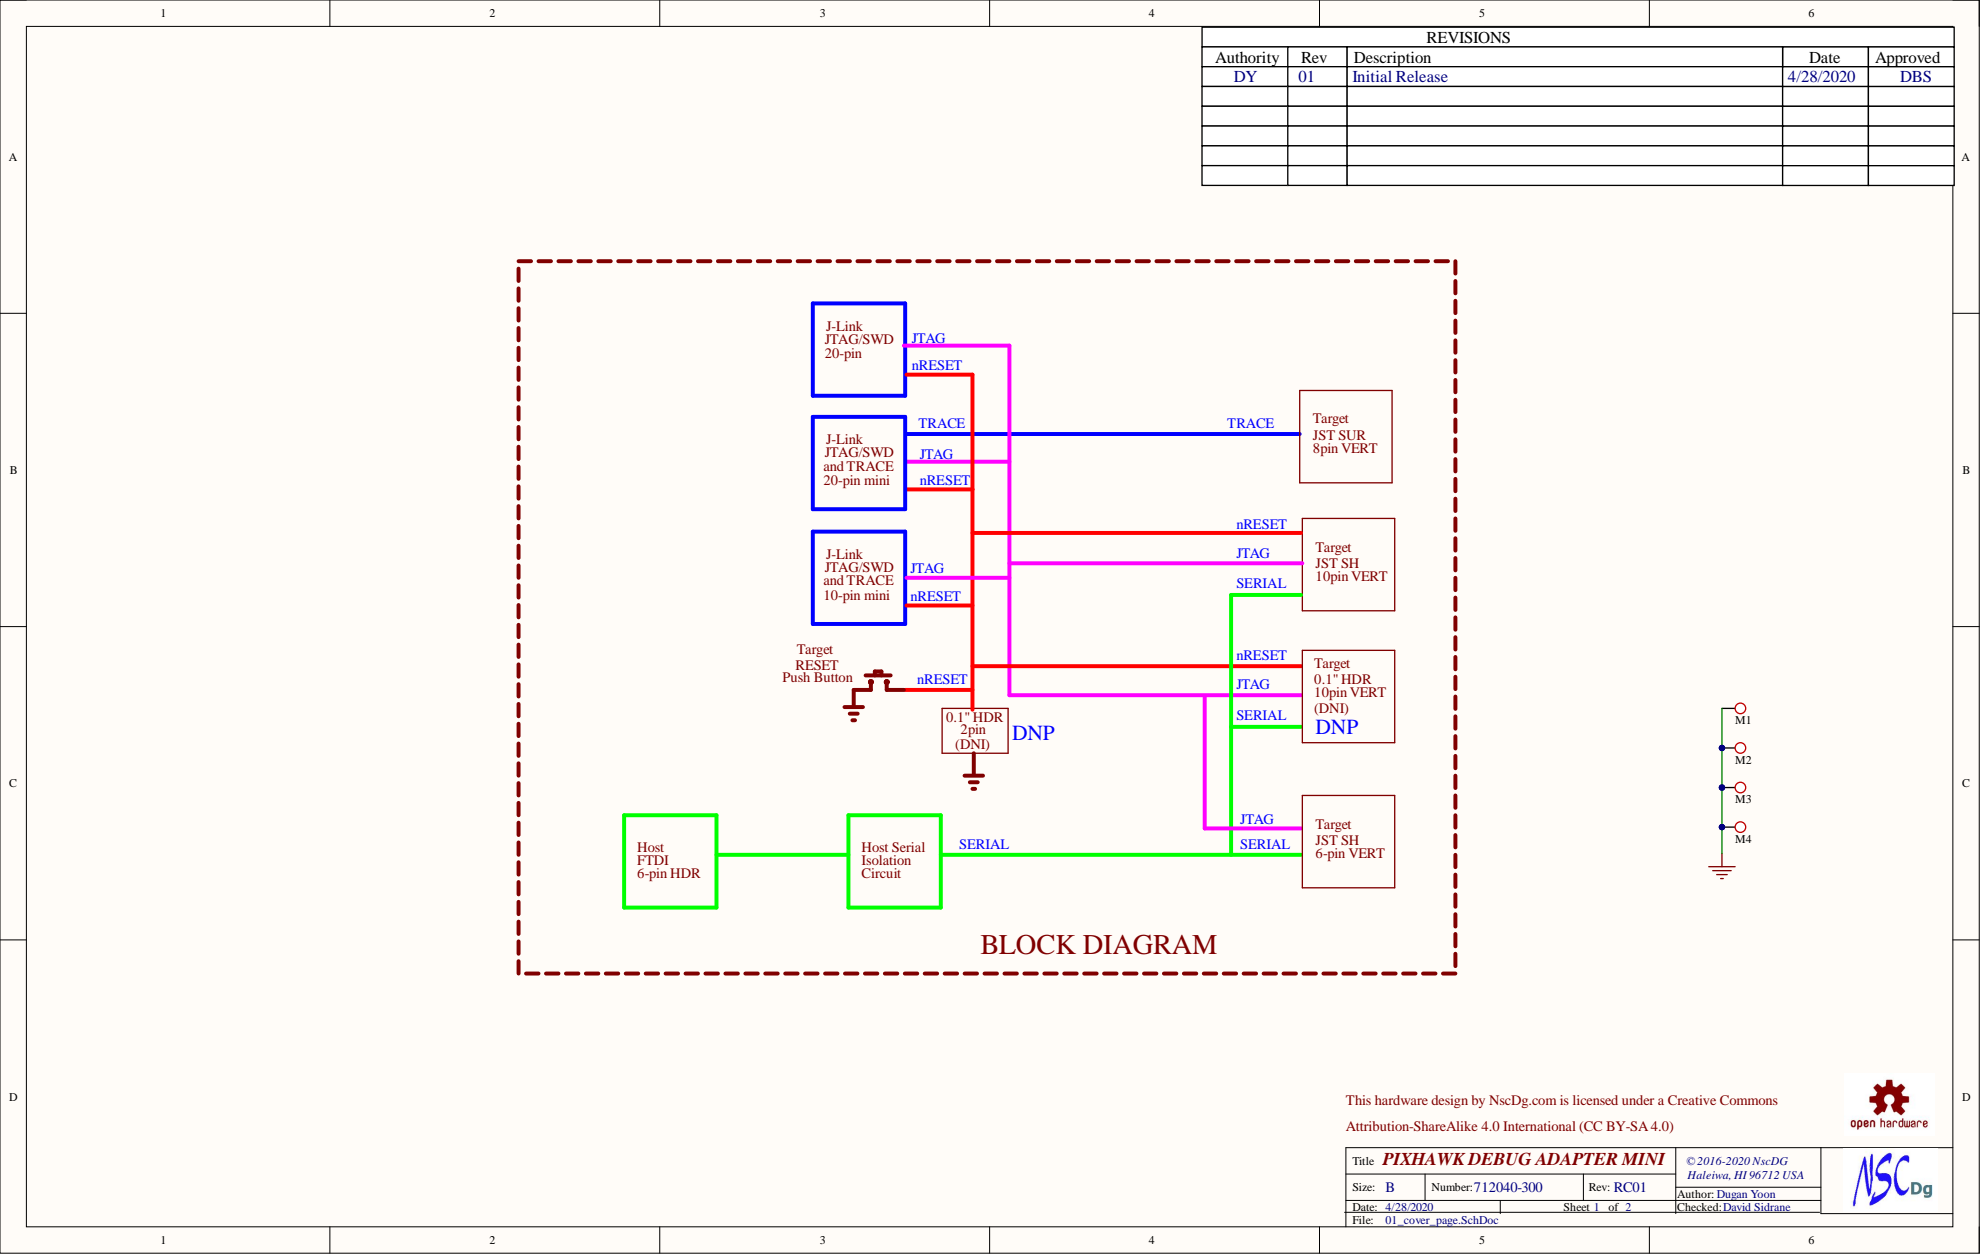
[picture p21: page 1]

Authority | Rev | Description | Date | Approved
DY | 01 | Initial Release | 4/28/2020 | DBS

J-Link
JTAG/SWD
20-pin mini and TRACE

JTAG

nRESET

10-pin mini and TRACE

SERIAL

This hardware design by NscDg.com is licensed under a Creative Commons

Attribution-ShareAlike 4.0 International (CC BY-SA 4.0)
PIXHAWK DEBUG ADAPTER MINI
Title

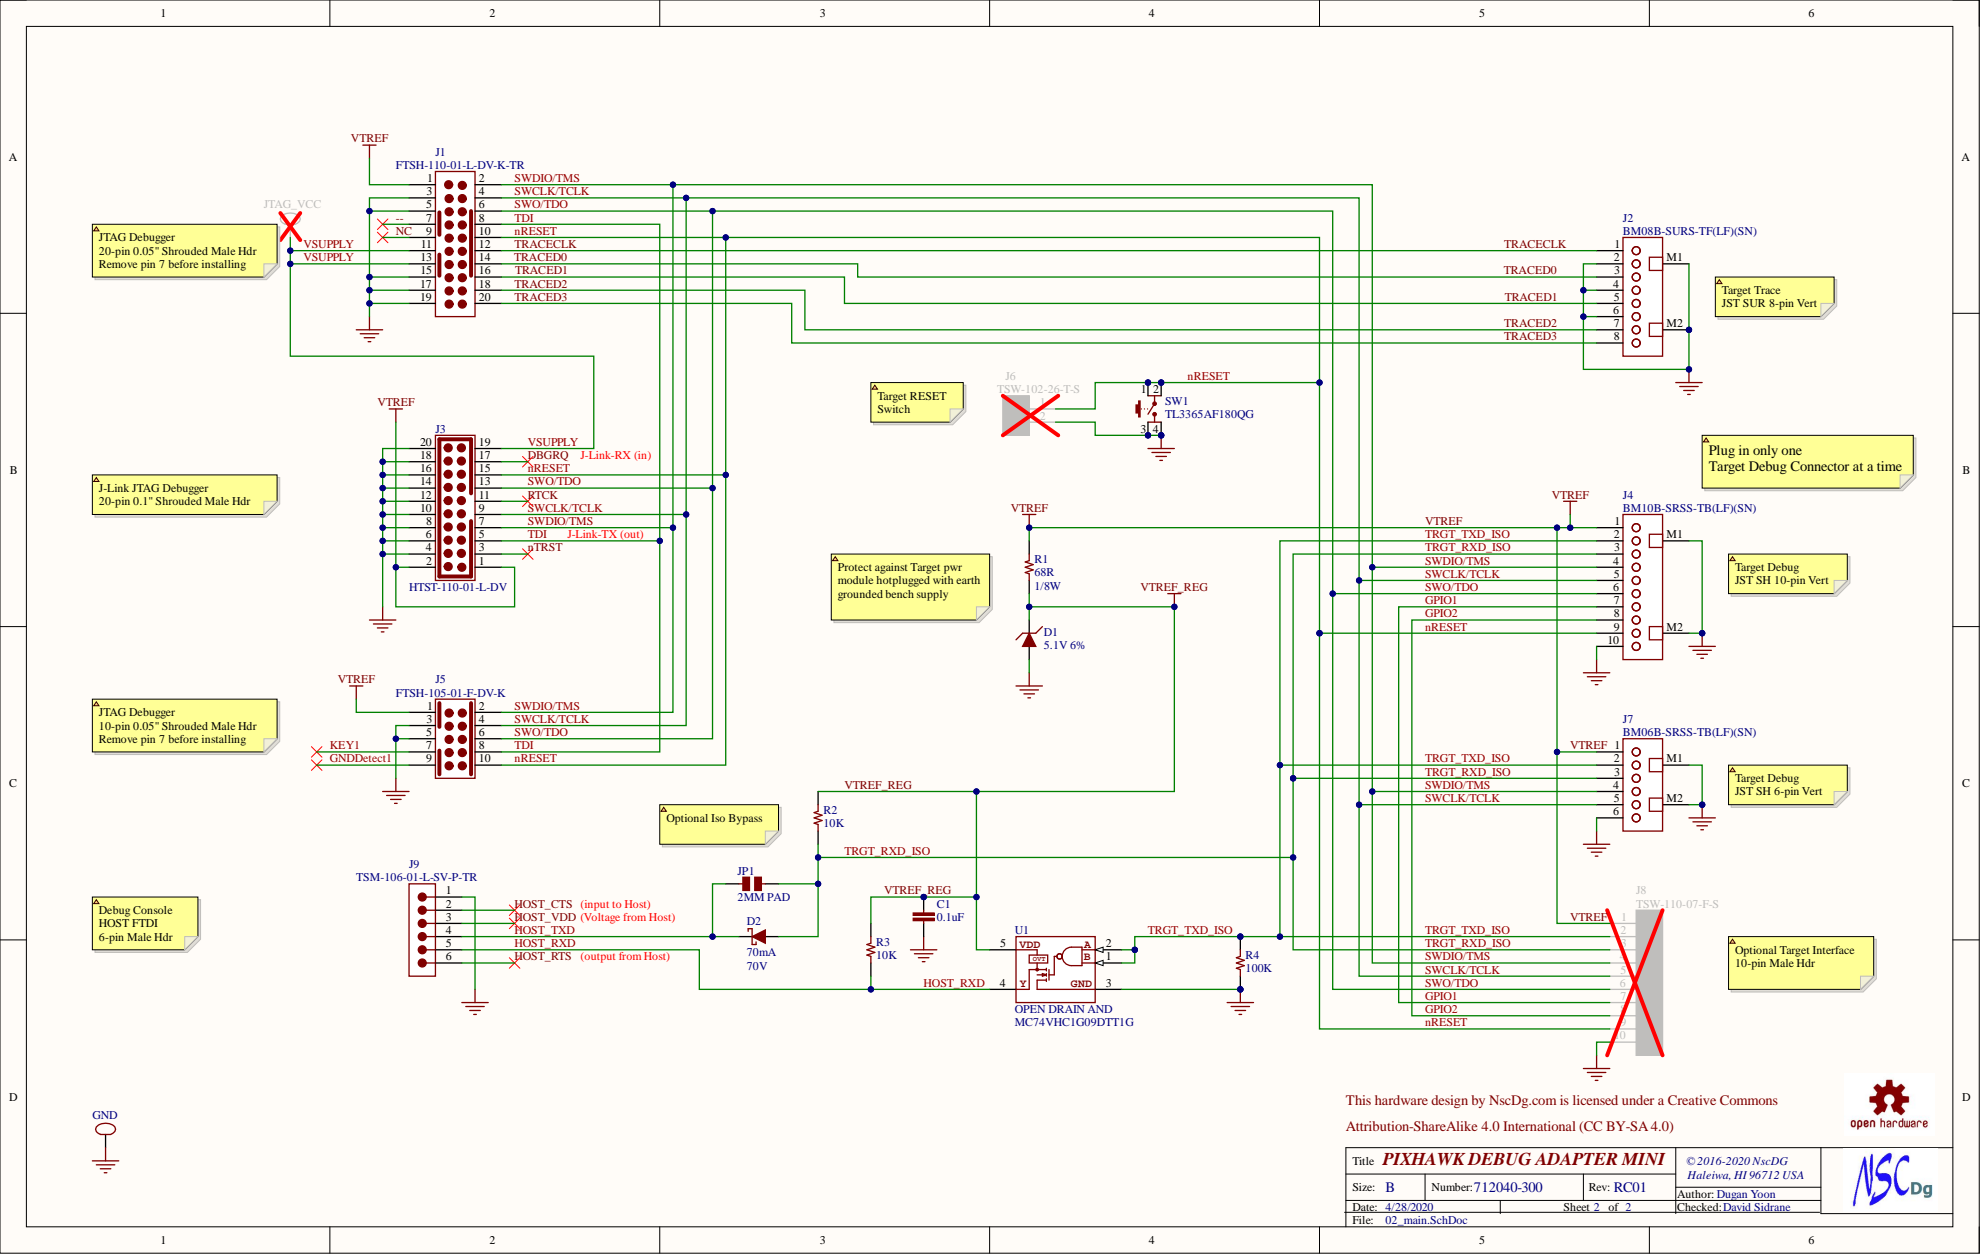
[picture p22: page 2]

SWCLK/TCLK

5 | | 6 | SWO/TDO

JTAG Debugger
20-pin 0.05" Shrouded Male Hdr
Remove pin 7 before installing

17 | 18 | TRACED2 | | | 4
19 | 20 | TRACED3 | | TRACED1 | 5

Target Trace
JST SUR 8-pin Vert

VTREF | | | | TRACED2 | 6

TRACED3 | 8

VSUPPLY J-Link-RX (in) | J6 nRESET | VTREF

Plug in only one
Target Debug Connector at a time

18 | 17 15 | DBGRQ nRESET
16
14 | 13 | SWO/TDO
12 | 11 9 | RTCK SWCLK/TCLK
10

J-Link JTAG Debugger
20-pin 0.1" Shrouded Male Hdr

Protect against Target pwr
module hotplugged with earth
grounded bench supply

Target Debug
JST SH 10-pin Vert

SWDIO/TMS | | | | GPIO1 | 7

GPIO2 | | 8
nRESET | | 9
TRGT_TXD_ISO | 10

10-pin 0.05" Shrouded Male Hdr

5 | 6 | SWO/TDO

TDI

TRGT_RXD_ISO | 3 | M2
SWDIO/TMS | 4
SWCLK/TCLK | 5
TRGT_TXD_ISO | 6

JST SH 6-pin Vert

B | 1 | SWDIO/TMS | 4

SWO/TDO | 6
GPIO1 | 7
GPIO2 | 8

This hardware design by NscDg.com is licensed under a Creative Commons

Attribution-ShareAlike 4.0 International (CC BY-SA 4.0)
PIXHAWK DEBUG ADAPTER MINI
Title

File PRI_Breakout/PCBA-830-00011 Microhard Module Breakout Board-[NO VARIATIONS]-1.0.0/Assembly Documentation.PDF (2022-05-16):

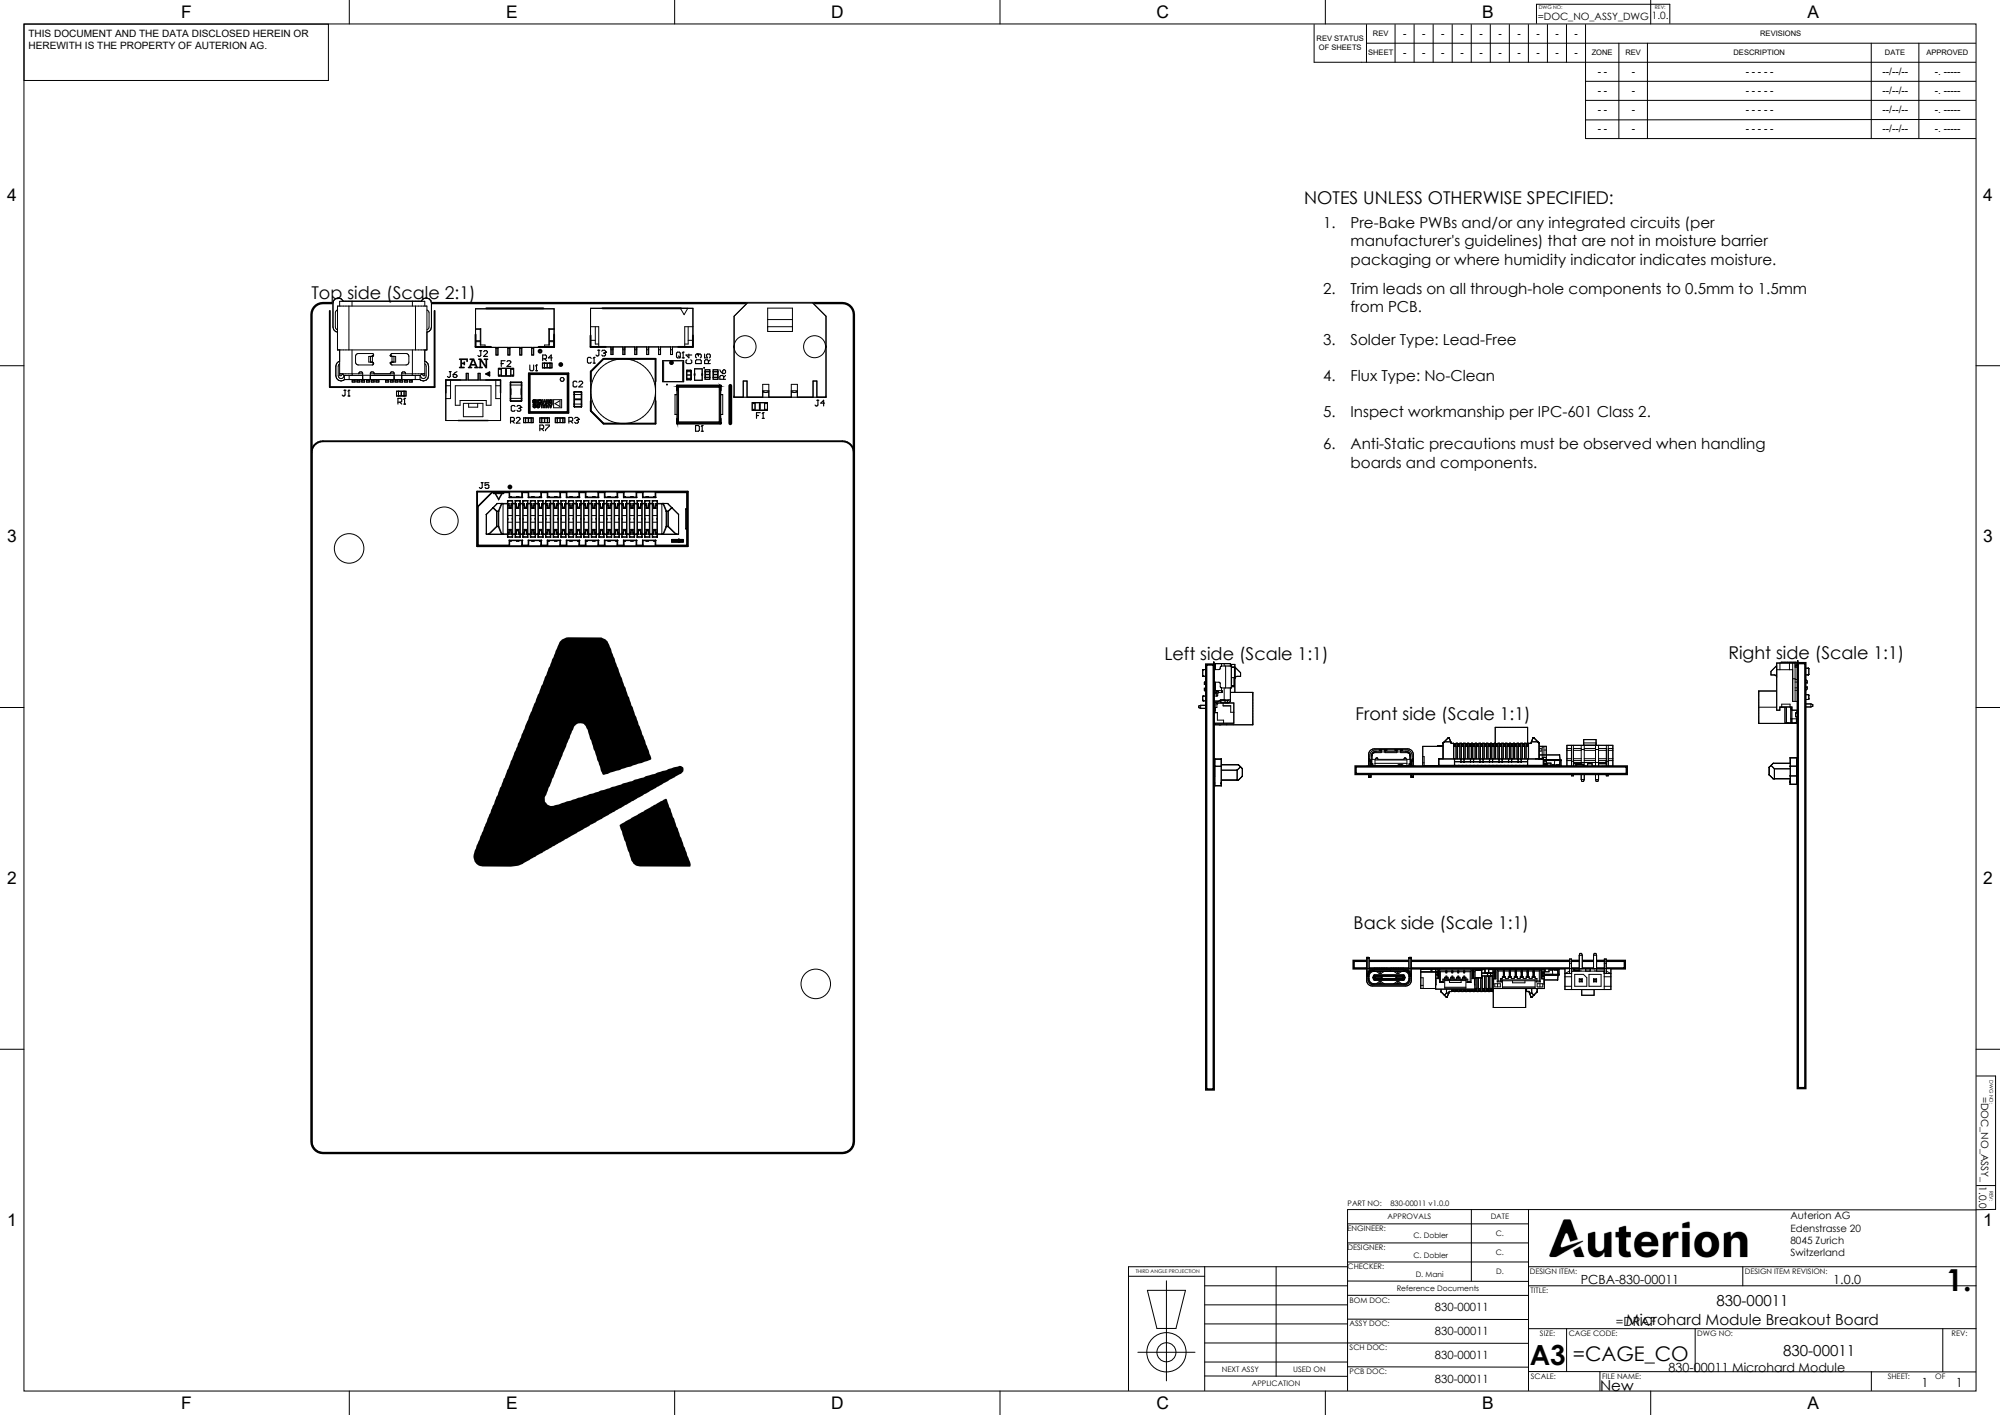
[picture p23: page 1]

THIS DOCUMENT AND THE DATA DISCLOSED HEREIN OR
HEREWITH IS THE PROPERTY OF AUTERION AG.

NOTES UNLESS OTHERWISE SPECIFIED:
Pre-Bake PWBs and/or any integrated circuits (per
manufacturer's guidelines) that are not in moisture barrier
packaging or where humidity indicator indicates moisture.
Trim leads on all through-hole components to 0.5mm to 1.5mm
from PCB.
3. Solder Type: Lead-Free

4. Flux Type: No-Clean

5. Inspect workmanship per IPC-601 Class 2.
Anti-Static precautions must be observed when handling
boards and components.

Microhard Module Breakout Board
=DRAF

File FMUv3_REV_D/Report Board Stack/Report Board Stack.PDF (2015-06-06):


Stack Up | Layer Stack
Layer | Board Layer Stack | Name | Material | Thickness | Constant
1 | | Top Paste
2 | | Top Overlay
3 | | Top Solder | Solder Resist (Black Matte) | 0.010mm | 3.5
4 | | Top | Copper | 0.035mm
5 | | Dielectric 1 | FR-4 | 0.150mm | 4.8
6 | | GND_top | Copper | 0.035mm
7 | | Dielectric 2 | FR-4 | 0.250mm | 4.8
8 | | HorizontalTop | Copper | 0.035mm
9 | | Dielectric 3 | FR-4 | 0.150mm | 4.8
10 | | Verticall_top | Copper | 0.035mm
11 | | Dielectric 4 | FR-4 | 0.250mm | 4.8
12 | | Horizontal_bot | Copper | 0.035mm
13 | | Dielectric 5 | FR-4 | 0.150mm | 4.8
14 | | VerticalBot | Copper | 0.035mm
15 | | Dielectric 6 | FR-4 | 0.250mm | 4.8
16 | | GND_BOT | Copper | 0.035mm
17 | | Dielectric 7 | FR-4 | 0.150mm | 4.8
18 | | Bottom | Copper | 0.035mm
19 | | Bottom Solder | Solder Resist (Black Matte) | 0.010mm | 3.5
20 | | Bottom Overlay
21 | | Bottom Paste

Height : 1.650mm







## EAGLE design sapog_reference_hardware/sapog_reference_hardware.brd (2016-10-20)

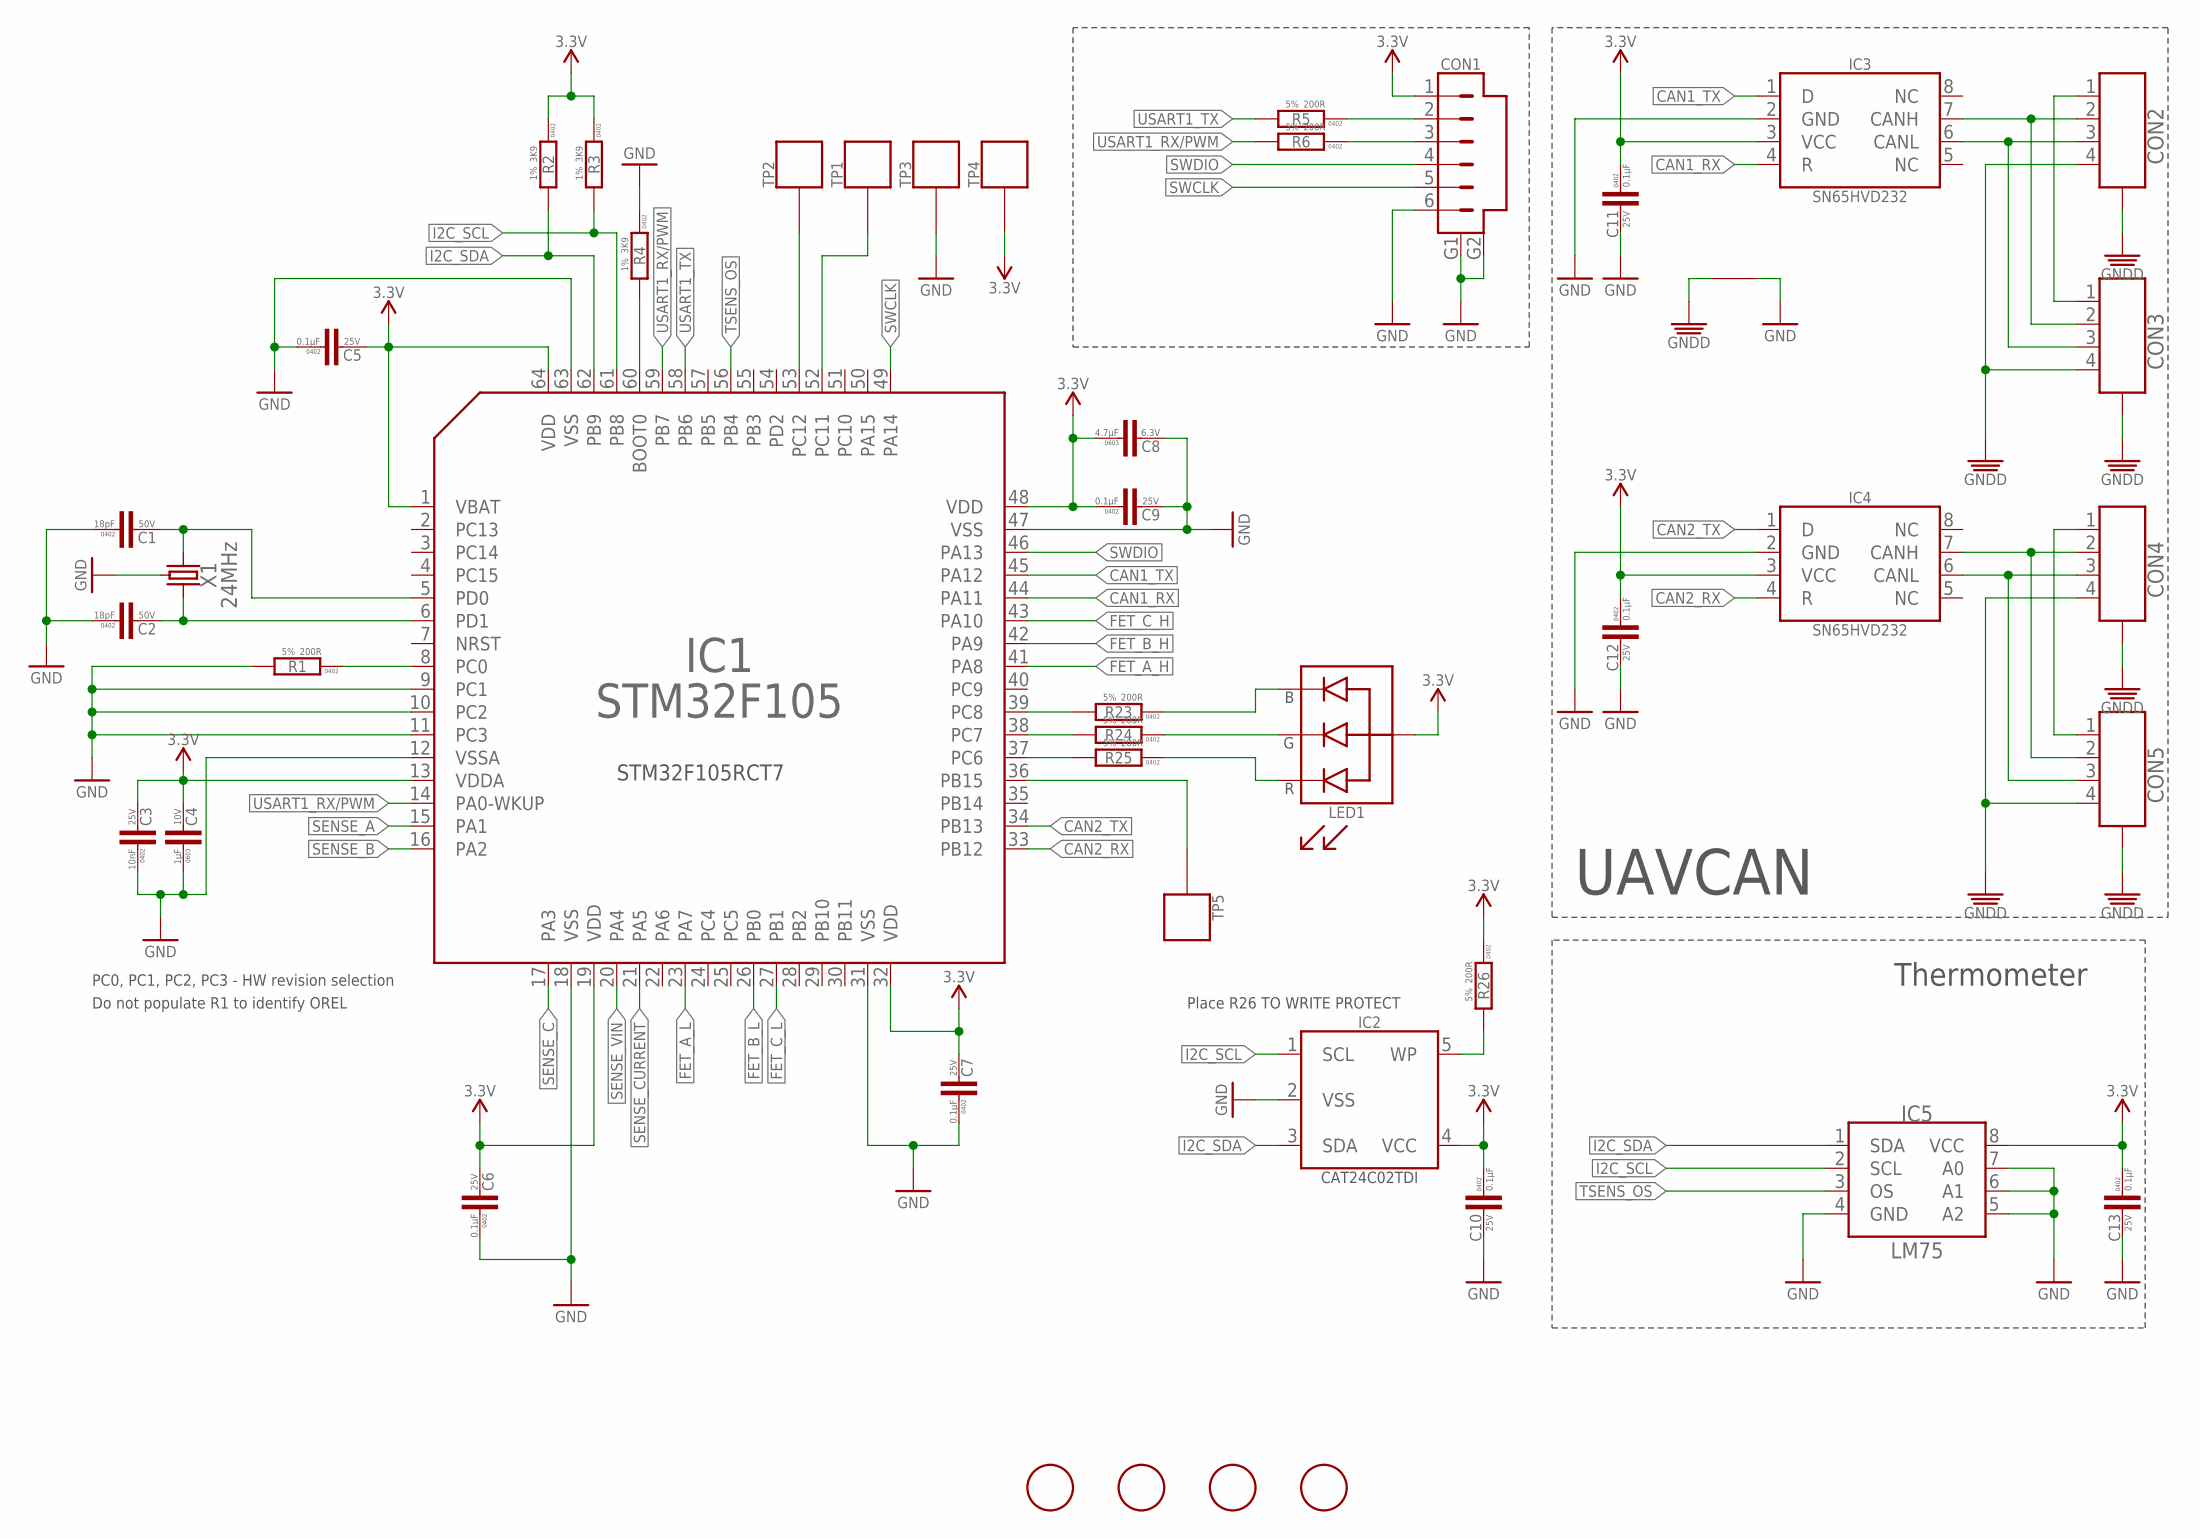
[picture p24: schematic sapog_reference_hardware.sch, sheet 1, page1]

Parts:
C1, C2: 18pF; C0402
C3: 10nF; C0402
C4: 1µF; C0603
C5, C6, C7, C9, C10, C11, C12, C13: 0.1µF; C0402
C8: 4.7µF; C0603
CON1: SM06B-SRSS-TB; SM06B; PARTNO SM06B-SRSS-TB
CON2, CON3, CON4, CON5: CON-4P-RA-JST_GH; JST_GH-4P-RA
FD1, FD2, FD3, FD4: FIDUCIALMOUNT; FIDUCIA-MOUNT
IC1: STM32F105; TQFP64-10X10; DIGIKEY# 497-11547-ND
IC2: CAT24C02; SOT23-5L
IC3, IC4: SN65HVD232D; SOIC8
IC5: LM75BD-TSSOP8; TSSOP8
LED1: LTST-C19HE1WT; LITE_ON_RGB_LED
R1: 200R; R0402
R2, R3, R4: 3K9; R0402
R5, R6, R23, R24, R25, R26: 200R; R0402; PARTNO RC0402FR-07240RL
TP1, TP2, TP3, TP4, TP5: PAD.05; PAD.05X.05; PARTNO *
U$2: CONNECTION
X1: 24MHz; OSCILLATOR-3.2X2.5; DIGIKEY# 1253-1198-1-ND

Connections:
BOOT0: IC1.60 (BOOT0), R4.2
CAN1_RX: IC1.44 (PA11), IC3.4 (R)
CAN1_TX: IC1.45 (PA12), IC3.1 (D)
CAN2_RX: IC1.33 (PB12), IC4.4 (R)
CAN2_TX: IC1.34 (PB13), IC4.1 (D)
FET_A_H: IC1.41 (PA8); also elsewhere on the board
FET_A_L: IC1.23 (PA7); also elsewhere on the board
FET_B_H: IC1.42 (PA9); also elsewhere on the board
FET_B_L: IC1.26 (PB0); also elsewhere on the board
FET_C_H: IC1.43 (PA10); also elsewhere on the board
FET_C_L: IC1.27 (PB1); also elsewhere on the board
GND: C1.1, C2.1, C3.1, C4.P$1 (1), C5.1, C6.1, C7.1, C8.P$2 (2), C9.2, C10.2, C11.2, C12.2, C13.2, CON1.6, CON1.G1, CON1.G2, IC1.9 (PC1), IC1.10 (PC2), IC1.11 (PC3), IC1.12 (VSSA), IC1.18 (VSS), IC1.31 (VSS), IC1.47 (VSS), IC1.63 (VSS), IC2.2 (VSS), IC3.2 (GND), IC4.2 (GND), IC5.4 (GND), IC5.5 (A2), IC5.6 (A1), IC5.7 (A0), R1.2, R4.1, TP3.P$1, U$2.P$2, X1.2 (GND), X1.4 (GND); also elsewhere on the board
GNDD: CON2.4, CON2.M$0 (GND), CON2.M$1 (GND), CON3.4, CON3.M$0 (GND), CON3.M$1 (GND), CON4.4, CON4.M$0 (GND), CON4.M$1 (GND), CON5.4, CON5.M$0 (GND), CON5.M$1 (GND), U$2.P$1
I2C_SCL: IC1.61 (PB8), IC2.1 (SCL), IC5.2 (SCL), R3.2
I2C_SDA: IC1.62 (PB9), IC2.3 (SDA), IC5.1 (SDA), R2.2
unnamed: CON1.2, R5.1
unnamed: CON1.3, R6.1
unnamed: IC1.37 (PC6), R25.2
unnamed: LED1.B, R23.1
unnamed: LED1.R, R25.1
unnamed: IC1.8 (PC0), R1.1
unnamed: IC2.5 (WP), R26.2
unnamed: IC1.38 (PC7), R24.2
unnamed: C1.2, IC1.5 (PD0), X1.3 (2)
unnamed: IC1.39 (PC8), R23.2
unnamed: CON4.1, CON5.1
unnamed: CON4.2, CON5.2, IC4.7 (CANH)
unnamed: C2.2, IC1.6 (PD1), X1.1
unnamed: CON2.1, CON3.1
unnamed: CON2.2, CON3.2, IC3.7 (CANH)
unnamed: CON4.3, CON5.3, IC4.6 (CANL)
unnamed: CON2.3, CON3.3, IC3.6 (CANL)
unnamed: LED1.G, R24.1
unnamed: IC1.53 (PC12), TP2.P$1
unnamed: IC1.36 (PB15), TP5.P$1
unnamed: IC1.52 (PC11), TP1.P$1
SENSE_A: IC1.15 (PA1); also elsewhere on the board
SENSE_B: IC1.16 (PA2); also elsewhere on the board
SENSE_C: IC1.17 (PA3); also elsewhere on the board
SENSE_CURRENT: IC1.21 (PA5); also elsewhere on the board
SENSE_VIN: IC1.20 (PA4); also elsewhere on the board
SWCLK: CON1.5, IC1.49 (PA14)
SWDIO: CON1.4, IC1.46 (PA13)
TSENS_OS: IC1.56 (PB4), IC5.3 (OS)
USART1_RX/PWM: IC1.14 (PA0-WKUP), IC1.59 (PB7), R6.2
USART1_TX: IC1.58 (PB6), R5.2
VDD_3V3: C3.2, C4.P$2 (2), C5.2, C6.2, C7.2, C8.P$1 (1), C9.1, C10.1, C11.1, C12.1, C13.1, CON1.1, IC1.1 (VBAT), IC1.13 (VDDA), IC1.19 (VDD), IC1.32 (VDD), IC1.48 (VDD), IC1.64 (VDD), IC2.4 (VCC), IC3.3 (VCC), IC4.3 (VCC), IC5.8 (VCC), LED1.+ (A), R2.1, R3.1, R26.1, TP4.P$1; also elsewhere on the board

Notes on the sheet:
UAVCAN
PC0, PC1, PC2, PC3 - HW revision selection
Do not populate R1 to identify OREL
Thermometer
Place R26 TO WRITE PROTECT
STM32F105RCT7

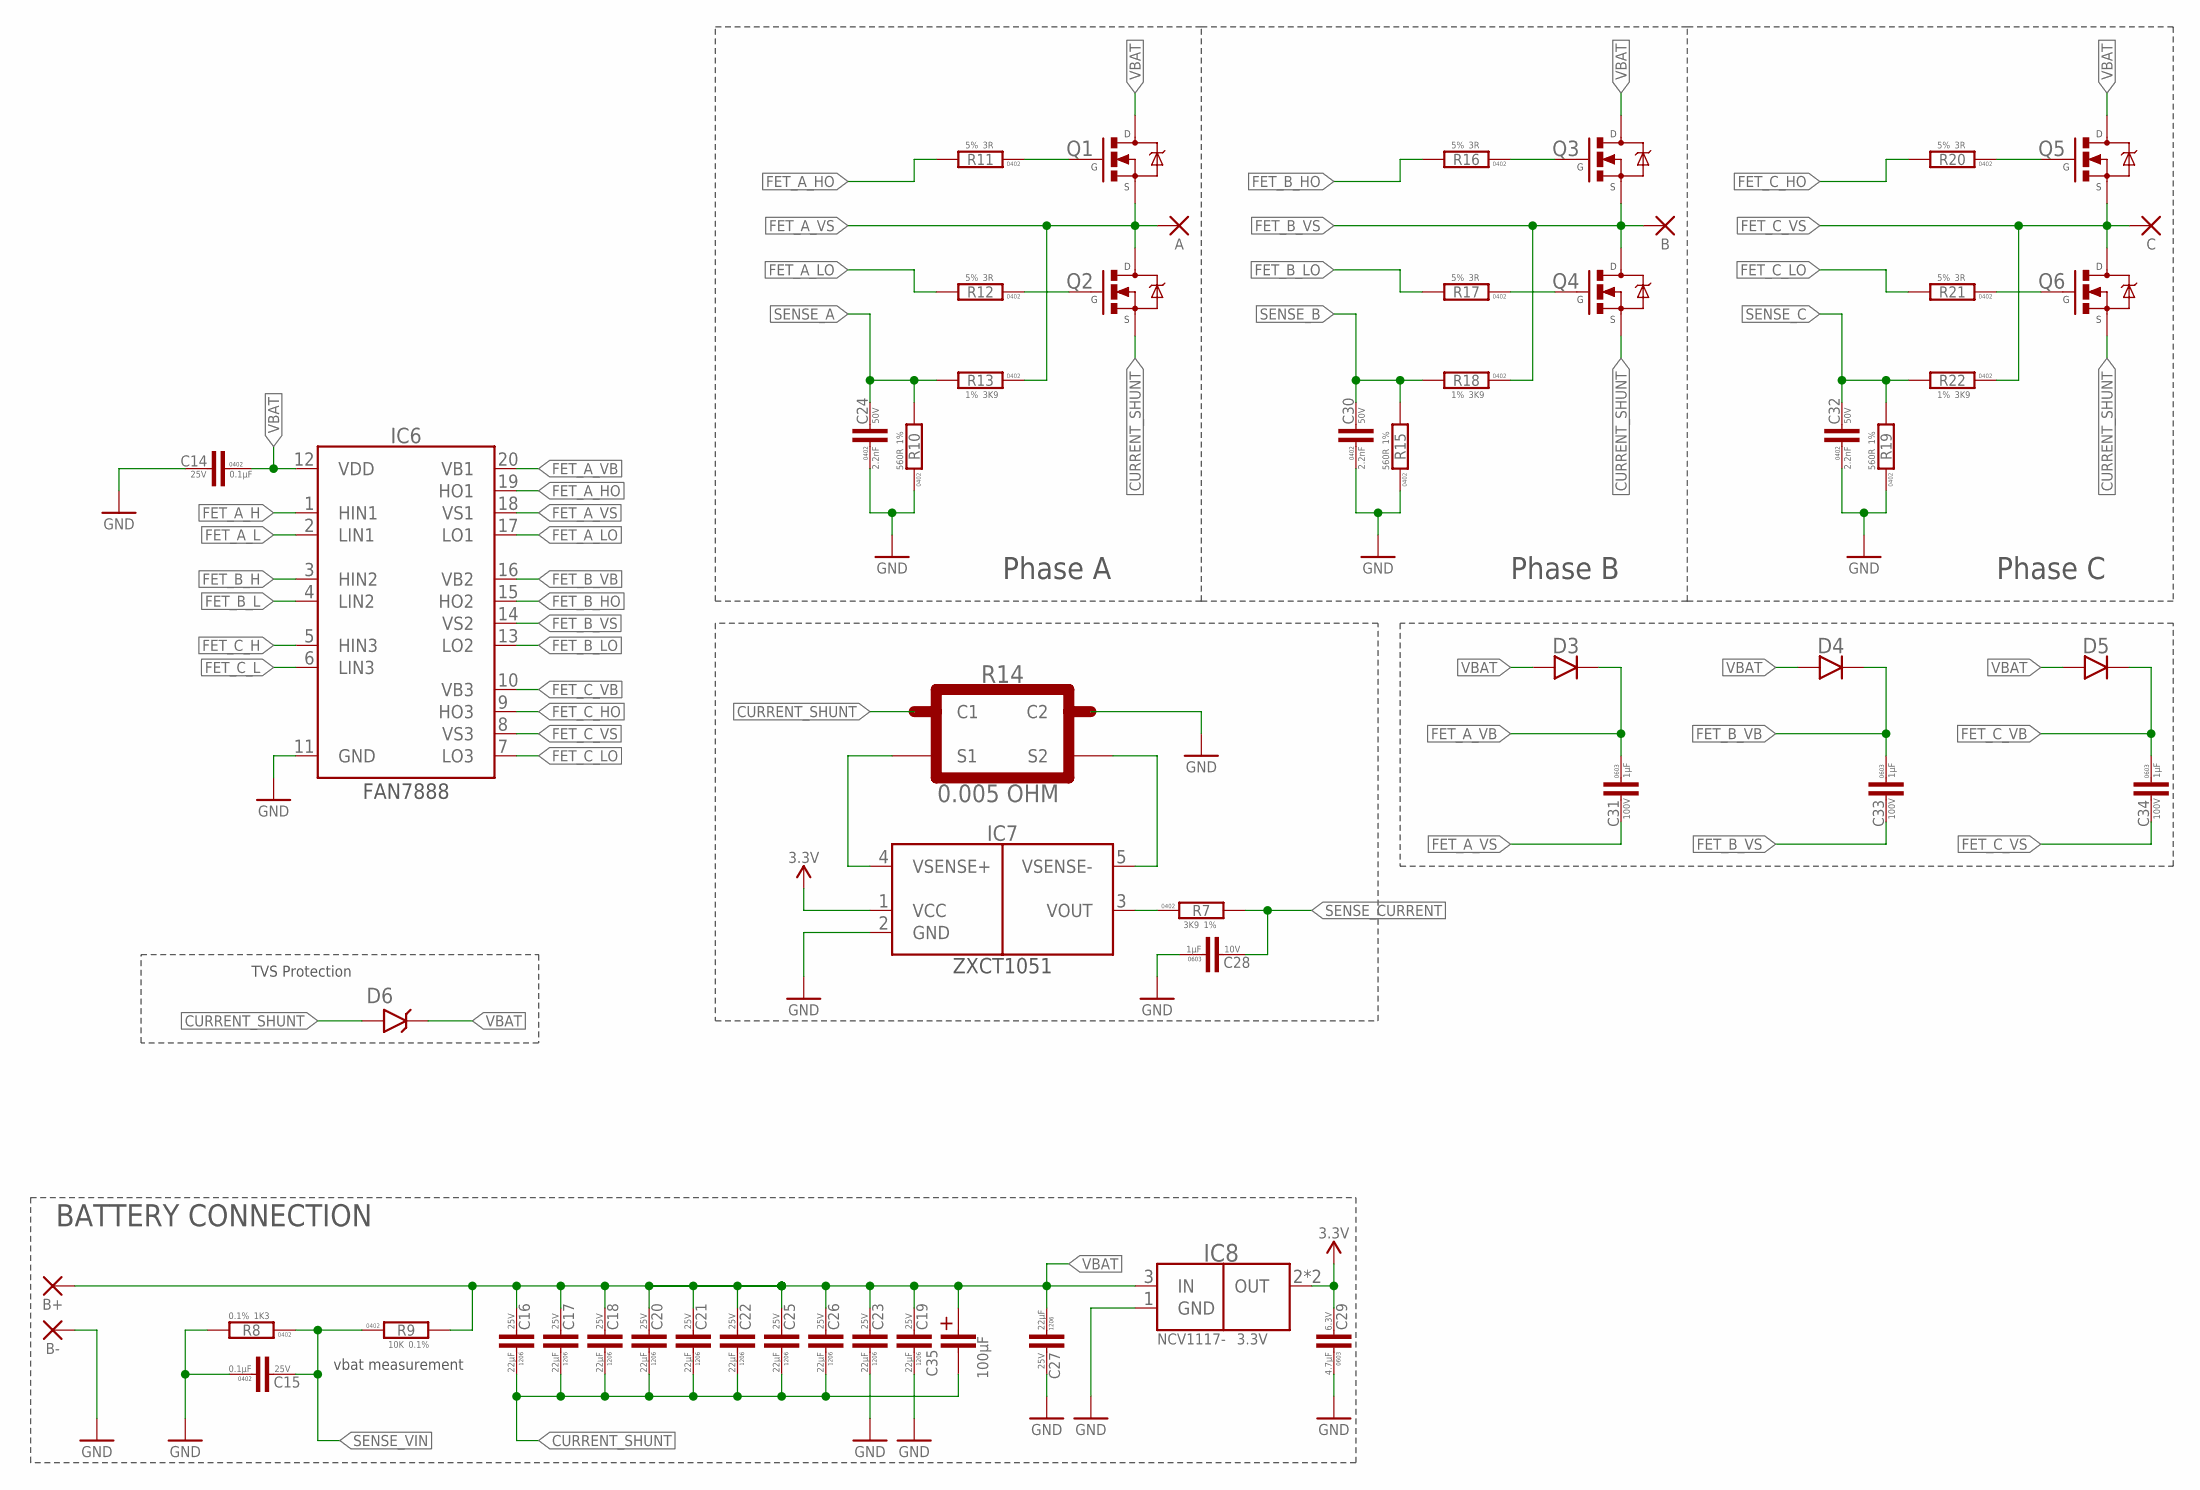
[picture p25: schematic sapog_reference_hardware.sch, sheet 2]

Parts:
A: WIREPADSMD5-2,5; 5-2,5
B: WIREPADSMD5-2,5; 5-2,5
B+: WIREPADSMD5-2,5; 5-2,5
B-: WIREPADSMD5-2,5; 5-2,5
C: WIREPADSMD5-2,5; 5-2,5
C14, C15: 0.1µF; C0402
C16, C17, C18, C19, C20, C21, C22, C23, C25, C26, C27: 22µF; C1206
C24, C30, C32: 2.2nF; C0402
C28, C31, C33, C34: 1µF; C0603
C29: 4.7µF; C0603
C35: 100µF; 3024
D3, D4, D5: BAS21AHT1G; SOD323
D6: 1KSMB20A; SMB
IC6: FAN7888; SOIC20; PARTNO FAN7888MX
IC7: ZXCT1051; SOT23-5L
IC8: 3.3V; SOT-223
Q1, Q2, Q3, Q4, Q5, Q6: BSC019N04NS-DFN5X6; DFN5X6
R7, R13, R18, R22: 3K9; R0402
R8: 1K3; R0402
R9: 10K; R0402
R10, R15, R19: 560R; R0402
R11, R12, R16, R17, R20, R21: 3R; R0402
R14: 0.005 OHM; 2010_CURRENT_SHUNT

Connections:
BLABLA: IC7.3 (VOUT), R7.1
CURRENT_SHUNT: C16.P$1 (1), C17.P$1 (1), C18.P$1 (1), C20.P$1 (1), C21.P$1 (1), C22.P$1 (1), C25.P$1 (1), C26.P$1 (1), C35.-, D6.A, Q2.1S (S), Q2.2S (S), Q2.3S (S), Q4.1S (S), Q4.2S (S), Q4.3S (S), Q6.1S (S), Q6.2S (S), Q6.3S (S), R14.CURRENT1 (C1)
FET_A_H: IC6.1 (HIN1); also elsewhere on the board
FET_A_HO: IC6.19 (HO1), R11.2
FET_A_L: IC6.2 (LIN1); also elsewhere on the board
FET_A_LO: IC6.17 (LO1), R12.2
FET_A_VB: C31.P$1 (1), D3.C, IC6.20 (VB1)
FET_A_VS: A.1, C31.P$2 (2), IC6.18 (VS1), Q1.1S (S), Q1.2S (S), Q1.3S (S), Q2.5D (D), Q2.6D (D), Q2.7D (D), Q2.8D (D), R13.1
FET_B_H: IC6.3 (HIN2); also elsewhere on the board
FET_B_HO: IC6.15 (HO2), R16.2
FET_B_L: IC6.4 (LIN2); also elsewhere on the board
FET_B_LO: IC6.13 (LO2), R17.2
FET_B_VB: C33.P$1 (1), D4.C, IC6.16 (VB2)
FET_B_VS: B.1, C33.P$2 (2), IC6.14 (VS2), Q3.1S (S), Q3.2S (S), Q3.3S (S), Q4.5D (D), Q4.6D (D), Q4.7D (D), Q4.8D (D), R18.1
FET_C_H: IC6.5 (HIN3); also elsewhere on the board
FET_C_HO: IC6.9 (HO3), R20.2
FET_C_L: IC6.6 (LIN3); also elsewhere on the board
FET_C_LO: IC6.7 (LO3), R21.2
FET_C_VB: C34.P$1 (1), D5.C, IC6.10 (VB3)
FET_C_VS: C.1, C34.P$2 (2), IC6.8 (VS3), Q5.1S (S), Q5.2S (S), Q5.3S (S), Q6.5D (D), Q6.6D (D), Q6.7D (D), Q6.8D (D), R22.1
GND: B-.1, C14.2, C15.1, C19.P$1 (1), C23.P$1 (1), C24.1, C27.P$2 (2), C28.P$1 (1), C29.P$1 (1), C30.1, C32.1, IC6.11 (GND), IC7.2 (GND), IC8.1 (GND), R8.2, R10.1, R14.CURRENT2 (C2), R15.1, R19.1; also elsewhere on the board
unnamed: Q2.4G (G), R12.1
unnamed: Q3.4G (G), R16.1
unnamed: Q4.4G (G), R17.1
unnamed: Q5.4G (G), R20.1
unnamed: IC7.5 (VSENSE-), R14.SENSE2 (S2)
unnamed: Q1.4G (G), R11.1
unnamed: IC7.4 (VSENSE+), R14.SENSE1 (S1)
unnamed: Q6.4G (G), R21.1
SENSE_A: C24.2, R10.2, R13.2; also elsewhere on the board
SENSE_B: C30.2, R15.2, R18.2; also elsewhere on the board
SENSE_C: C32.2, R19.2, R22.2; also elsewhere on the board
SENSE_CURRENT: C28.P$2 (2), R7.2; also elsewhere on the board
SENSE_VIN: C15.2, R8.1, R9.1; also elsewhere on the board
VBAT: B+.1, C14.1, C16.P$2 (2), C17.P$2 (2), C18.P$2 (2), C19.P$2 (2), C20.P$2 (2), C21.P$2 (2), C22.P$2 (2), C23.P$2 (2), C25.P$2 (2), C26.P$2 (2), C27.P$1 (1), C35.+, D3.A, D4.A, D5.A, D6.C, IC6.12 (VDD), IC8.3 (IN), Q1.5D (D), Q1.6D (D), Q1.7D (D), Q1.8D (D), Q3.5D (D), Q3.6D (D), Q3.7D (D), Q3.8D (D), Q5.5D (D), Q5.6D (D), Q5.7D (D), Q5.8D (D), R9.2
VDD_3V3: C29.P$2 (2), IC7.1 (VCC), IC8.2 (OUT), IC8.4 (OUT); also elsewhere on the board

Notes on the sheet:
vbat measurement
BATTERY CONNECTION
Phase A
Phase B
Phase C
TVS Protection

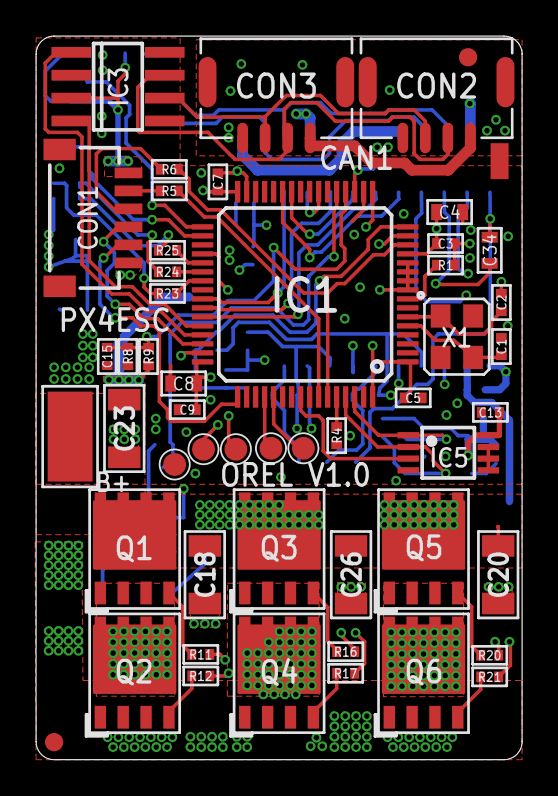
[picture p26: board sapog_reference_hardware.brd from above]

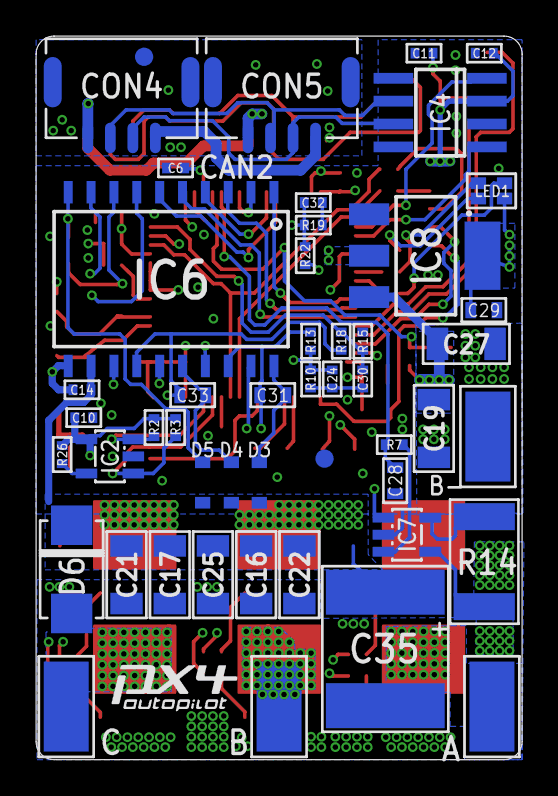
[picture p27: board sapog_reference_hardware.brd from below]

Board: 4 copper layers, 27.0 x 40.2 mm, 103 parts (50 on the bottom side), 70 nets.

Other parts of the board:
U$1: REF_BOARD_OUTLINE
U$3: PX4-LOGO-7MM

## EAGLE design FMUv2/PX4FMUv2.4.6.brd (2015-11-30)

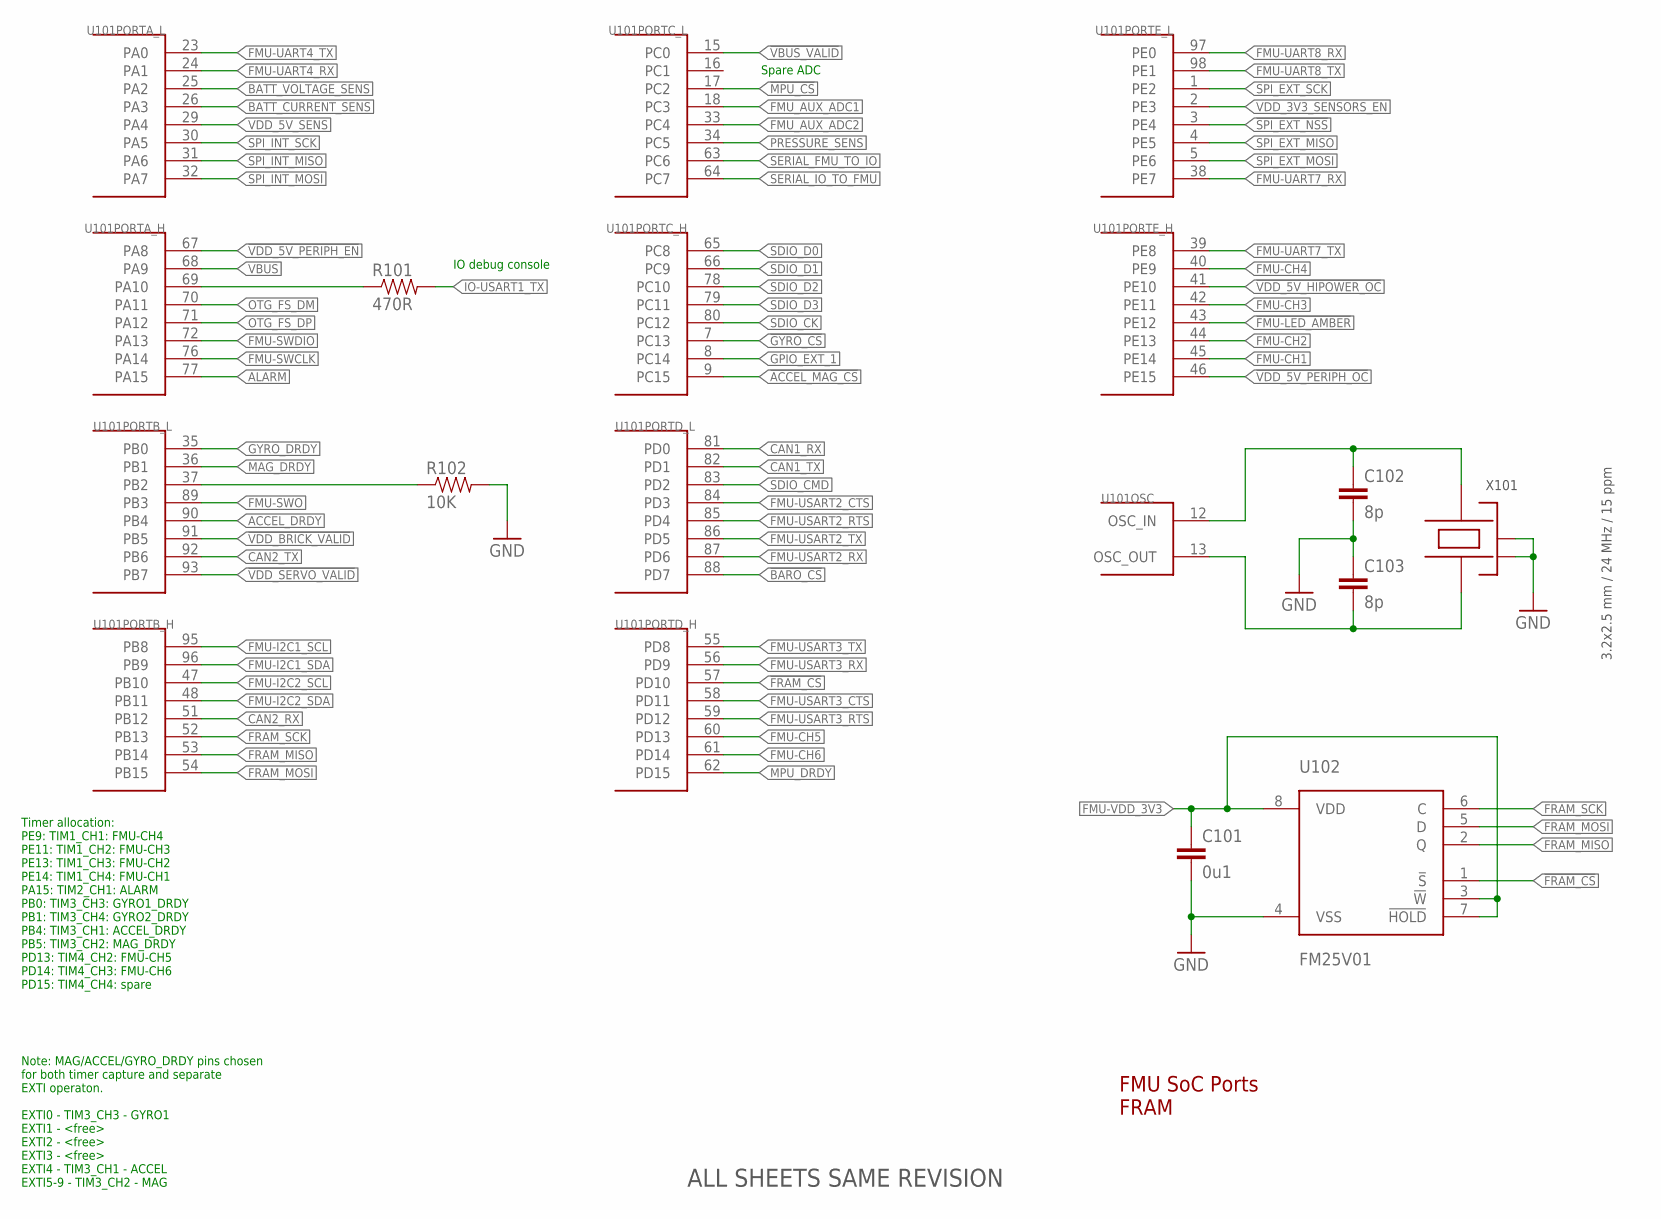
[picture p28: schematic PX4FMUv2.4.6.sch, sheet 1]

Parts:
C101: 0u1; 0402-CAP; PARTNO CC0402ZRY5V7BB104
C102, C103: 8p; 0402-CAP; PARTNO C1005C0G1H080C
R101: 470R; 0402-RES; PARTNO RC0402FR-07470RL
R102: 10K; 0402-RES; PARTNO RC0402FR-0710KL
U101: STM32F4X7VX; TQFP100; PARTNO STM32F427VI
U102: FM25V01; SO08; PARTNO FM25V01-G
X101: 3.2x2.5 mm / 24 MHz / 15 ppm; OSCILLATOR-3.2X2.5; PARTNO NX3225SA-24.000000MHZ

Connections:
!ACCEL_MAG_CS: U101.9 (PC15); also elsewhere on the board
!BARO_CS: U101.88 (PD7); also elsewhere on the board
!FMU-LED_AMBER: U101.43 (PE12); also elsewhere on the board
!FRAM_CS: U101.57 (PD10), U102.1 (!S)
!GYRO_CS: U101.7 (PC13); also elsewhere on the board
!MPU_CS: U101.17 (PC2); also elsewhere on the board
!SPI_EXT_NSS: U101.3 (PE4); also elsewhere on the board
!VBUS_VALID: U101.15 (PC0); also elsewhere on the board
!VDD_5V_HIPOWER_OC: U101.41 (PE10); also elsewhere on the board
!VDD_5V_PERIPH_EN: U101.67 (PA8); also elsewhere on the board
!VDD_5V_PERIPH_OC: U101.46 (PE15); also elsewhere on the board
!VDD_BRICK_VALID: U101.91 (PB5); also elsewhere on the board
!VDD_SERVO_VALID: U101.93 (PB7); also elsewhere on the board
ACCEL_DRDY: U101.90 (PB4); also elsewhere on the board
ALARM: U101.77 (PA15); also elsewhere on the board
BATT_CURRENT_SENS: U101.26 (PA3); also elsewhere on the board
BATT_VOLTAGE_SENS: U101.25 (PA2); also elsewhere on the board
CAN1_RX: U101.81 (PD0); also elsewhere on the board
CAN1_TX: U101.82 (PD1); also elsewhere on the board
CAN2_RX: U101.51 (PB12); also elsewhere on the board
CAN2_TX: U101.92 (PB6); also elsewhere on the board
FMU-CH1: U101.45 (PE14); also elsewhere on the board
FMU-CH2: U101.44 (PE13); also elsewhere on the board
FMU-CH3: U101.42 (PE11); also elsewhere on the board
FMU-CH4: U101.40 (PE9); also elsewhere on the board
FMU-CH5: U101.60 (PD13); also elsewhere on the board
FMU-CH6: U101.61 (PD14); also elsewhere on the board
FMU-I2C1_SCL: U101.95 (PB8); also elsewhere on the board
FMU-I2C1_SDA: U101.96 (PB9); also elsewhere on the board
FMU-I2C2_SCL: U101.47 (PB10); also elsewhere on the board
FMU-I2C2_SDA: U101.48 (PB11); also elsewhere on the board
FMU-SWCLK: U101.76 (PA14); also elsewhere on the board
FMU-SWDIO: U101.72 (PA13); also elsewhere on the board
FMU-SWO: U101.89 (PB3); also elsewhere on the board
FMU-UART4_RX: U101.24 (PA1); also elsewhere on the board
FMU-UART4_TX: U101.23 (PA0); also elsewhere on the board
FMU-UART7_RX: U101.38 (PE7); also elsewhere on the board
FMU-UART7_TX: U101.39 (PE8); also elsewhere on the board
FMU-UART8_RX: U101.97 (PE0); also elsewhere on the board
FMU-UART8_TX: U101.98 (PE1); also elsewhere on the board
FMU-USART2_CTS: U101.84 (PD3); also elsewhere on the board
FMU-USART2_RTS: U101.85 (PD4); also elsewhere on the board
FMU-USART2_RX: U101.87 (PD6); also elsewhere on the board
FMU-USART2_TX: U101.86 (PD5); also elsewhere on the board
FMU-USART3_CTS: U101.58 (PD11); also elsewhere on the board
FMU-USART3_RTS: U101.59 (PD12); also elsewhere on the board
FMU-USART3_RX: U101.56 (PD9); also elsewhere on the board
FMU-USART3_TX: U101.55 (PD8); also elsewhere on the board
FMU-VDD_3V3: C101.P$1 (1), U102.3 (!W), U102.7 (!HOLD), U102.8 (VDD); also elsewhere on the board
FMU_AUX_ADC1: U101.18 (PC3); also elsewhere on the board
FMU_AUX_ADC2: U101.33 (PC4); also elsewhere on the board
FRAM_MISO: U101.53 (PB14), U102.2 (Q)
FRAM_MOSI: U101.54 (PB15), U102.5 (D)
FRAM_SCK: U101.52 (PB13), U102.6 (C)
GND: C101.P$2 (2), C102.P$2 (2), C103.P$1 (1), R102.P$2 (2), U102.4 (VSS), X101.2 (NC_2), X101.4 (NC_4); also elsewhere on the board
GPIO_EXT_1: U101.8 (PC14); also elsewhere on the board
GYRO_DRDY: U101.35 (PB0); also elsewhere on the board
IO-USART1_TX: R101.P$2 (2); also elsewhere on the board
MAG_DRDY: U101.36 (PB1); also elsewhere on the board
MPU_DRDY: U101.62 (PD15); also elsewhere on the board
unnamed: C103.P$2 (2), U101.13 (OSC_OUT), X101.1
unnamed: C102.P$1 (1), U101.12 (OSC_IN), X101.3
unnamed: R101.P$1 (1), U101.69 (PA10)
OTG_FS_DM: U101.70 (PA11); also elsewhere on the board
OTG_FS_DP: U101.71 (PA12); also elsewhere on the board
PB2-BOOT1: R102.P$1 (1), U101.37 (PB2)
PRESSURE_SENS: U101.34 (PC5); also elsewhere on the board
SDIO_CK: U101.80 (PC12); also elsewhere on the board
SDIO_CMD: U101.83 (PD2); also elsewhere on the board
SDIO_D0: U101.65 (PC8); also elsewhere on the board
SDIO_D1: U101.66 (PC9); also elsewhere on the board
SDIO_D2: U101.78 (PC10); also elsewhere on the board
SDIO_D3: U101.79 (PC11); also elsewhere on the board
SERIAL_FMU_TO_IO: U101.63 (PC6); also elsewhere on the board
SERIAL_IO_TO_FMU: U101.64 (PC7); also elsewhere on the board
SPI_EXT_MISO: U101.4 (PE5); also elsewhere on the board
SPI_EXT_MOSI: U101.5 (PE6); also elsewhere on the board
SPI_EXT_SCK: U101.1 (PE2); also elsewhere on the board
SPI_INT_MISO: U101.31 (PA6); also elsewhere on the board
SPI_INT_MOSI: U101.32 (PA7); also elsewhere on the board
SPI_INT_SCK: U101.30 (PA5); also elsewhere on the board
VBUS: U101.68 (PA9); also elsewhere on the board
VDD_3V3_SENSORS_EN: U101.2 (PE3); also elsewhere on the board
VDD_5V_SENS: U101.29 (PA4); also elsewhere on the board

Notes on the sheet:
FMU SoC Ports FRAM
Note: MAG/ACCEL/GYRO_DRDY pins chosen for both timer capture and separate EXTI operaton. EXTI0 - TIM3_CH3 - GYRO1 EXTI1 - <free> EXTI2 - <free> EXTI3 - <free> EXTI4 - TIM3_CH1 - ACCEL EXTI5-9 - TIM3_CH2 - MAG
Timer allocation: PE9: TIM1_CH1: FMU-CH4 PE11: TIM1_CH2: FMU-CH3 PE13: TIM1_CH3: FMU-CH2 PE14: TIM1_CH4: FMU-CH1 PA15: TIM2_CH1: ALARM PB0: TIM3_CH3: GYRO1_DRDY PB1: TIM3_CH4: GYRO2_DRDY PB4: TIM3_CH1: ACCEL_DRDY PB5: TIM3_CH2: MAG_DRDY PD13: TIM4_CH2: FMU-CH5 PD14: TIM4_CH3: FMU-CH6 PD15: TIM4_CH4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
IO debug console
Spare ADC
ALL SHEETS SAME REVISION

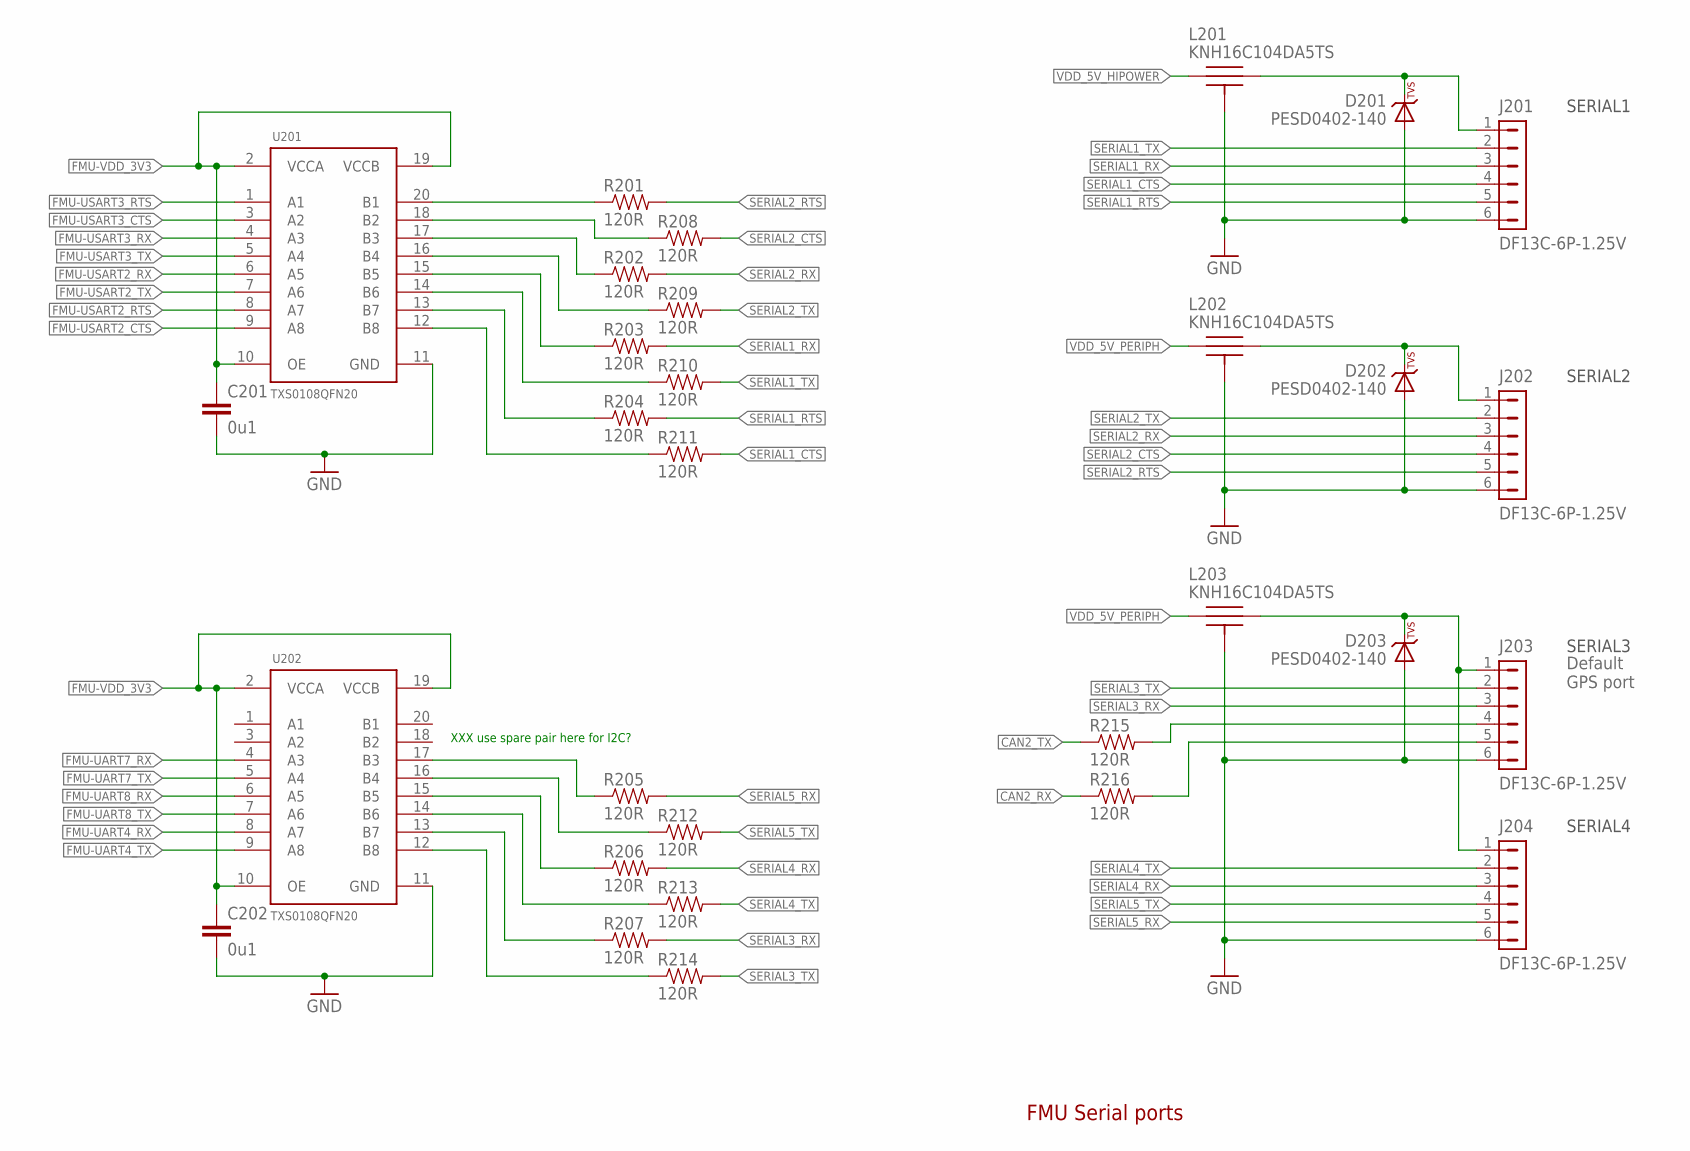
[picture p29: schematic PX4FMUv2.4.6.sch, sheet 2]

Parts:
C201, C202: 0u1; 0402-CAP; PARTNO CC0402ZRY5V7BB104
D201, D202, D203: PESD0402-140; 0402-TVS; PARTNO PESD0402-140
J201, J202, J203, J204: DF13C-6P-1.25V; PARTNO DF13C-6P-1.25V(20)
L201, L202, L203: KNH16C104DA5TS; KYOCERA-KNH16-DA; PARTNO KNH16C104DA5TS
R201, R202, R203, R204, R205, R206, R207, R208, R209, R210, R211, R212, R213, R214, R215, R216: 120R; 0402-RES; PARTNO RC0402FR-07120RL
U201, U202: TXS0108QFN20; QFN20-RGY; PARTNO TXS0108ERGYR

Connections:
CAN2_RX: R216.P$1 (1); also elsewhere on the board
CAN2_TX: R215.P$1 (1); also elsewhere on the board
FMU-UART4_RX: U202.8 (A7); also elsewhere on the board
FMU-UART4_TX: U202.9 (A8); also elsewhere on the board
FMU-UART7_RX: U202.4 (A3); also elsewhere on the board
FMU-UART7_TX: U202.5 (A4); also elsewhere on the board
FMU-UART8_RX: U202.6 (A5); also elsewhere on the board
FMU-UART8_TX: U202.7 (A6); also elsewhere on the board
FMU-USART2_CTS: U201.9 (A8); also elsewhere on the board
FMU-USART2_RTS: U201.8 (A7); also elsewhere on the board
FMU-USART2_RX: U201.6 (A5); also elsewhere on the board
FMU-USART2_TX: U201.7 (A6); also elsewhere on the board
FMU-USART3_CTS: U201.3 (A2); also elsewhere on the board
FMU-USART3_RTS: U201.1 (A1); also elsewhere on the board
FMU-USART3_RX: U201.4 (A3); also elsewhere on the board
FMU-USART3_TX: U201.5 (A4); also elsewhere on the board
FMU-VDD_3V3: C201.P$1 (1), C202.P$1 (1), U201.2 (VCCA), U201.10 (OE), U201.19 (VCCB), U202.2 (VCCA), U202.10 (OE), U202.19 (VCCB); also elsewhere on the board
GND: C201.P$2 (2), C202.P$2 (2), D201.A, D202.A, D203.A, J201.6, J202.6, J203.6, J204.6, L201.P$3, L201.P$4, L201.P$5, L202.P$3, L202.P$4, L202.P$5, L203.P$3, L203.P$4, L203.P$5, U201.11 (GND), U202.11 (GND); also elsewhere on the board
unnamed: D201.C, J201.1, L201.P$2
unnamed: J203.4, R215.P$2 (2)
unnamed: J203.5, R216.P$2 (2)
unnamed: R201.P$1 (1), U201.20 (B1)
unnamed: R208.P$1 (1), U201.18 (B2)
unnamed: R202.P$1 (1), U201.17 (B3)
unnamed: R209.P$1 (1), U201.16 (B4)
unnamed: R203.P$1 (1), U201.15 (B5)
unnamed: R210.P$1 (1), U201.14 (B6)
unnamed: R204.P$1 (1), U201.13 (B7)
unnamed: R211.P$1 (1), U201.12 (B8)
unnamed: R207.P$1 (1), U202.13 (B7)
unnamed: R214.P$1 (1), U202.12 (B8)
unnamed: R205.P$1 (1), U202.17 (B3)
unnamed: R212.P$1 (1), U202.16 (B4)
unnamed: R206.P$1 (1), U202.15 (B5)
unnamed: R213.P$1 (1), U202.14 (B6)
unnamed: D203.C, J203.1, J204.1, L203.P$2
unnamed: D202.C, J202.1, L202.P$2
SERIAL1_CTS: J201.4, R211.P$2 (2)
SERIAL1_RTS: J201.5, R204.P$2 (2)
SERIAL1_RX: J201.3, R203.P$2 (2); also elsewhere on the board
SERIAL1_TX: J201.2, R210.P$2 (2); also elsewhere on the board
SERIAL2_CTS: J202.4, R208.P$2 (2)
SERIAL2_RTS: J202.5, R201.P$2 (2)
SERIAL2_RX: J202.3, R202.P$2 (2); also elsewhere on the board
SERIAL2_TX: J202.2, R209.P$2 (2); also elsewhere on the board
SERIAL3_RX: J203.3, R207.P$2 (2); also elsewhere on the board
SERIAL3_TX: J203.2, R214.P$2 (2); also elsewhere on the board
SERIAL4_RX: J204.3, R206.P$2 (2); also elsewhere on the board
SERIAL4_TX: J204.2, R213.P$2 (2); also elsewhere on the board
SERIAL5_RX: J204.5, R205.P$2 (2); also elsewhere on the board
SERIAL5_TX: J204.4, R212.P$2 (2); also elsewhere on the board
VDD_5V_HIPOWER: L201.P$1; also elsewhere on the board
VDD_5V_PERIPH: L202.P$1, L203.P$1; also elsewhere on the board

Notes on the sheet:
FMU Serial ports
XXX use spare pair here for I2C?
SERIAL2
SERIAL1
SERIAL3
SERIAL4
Default GPS port

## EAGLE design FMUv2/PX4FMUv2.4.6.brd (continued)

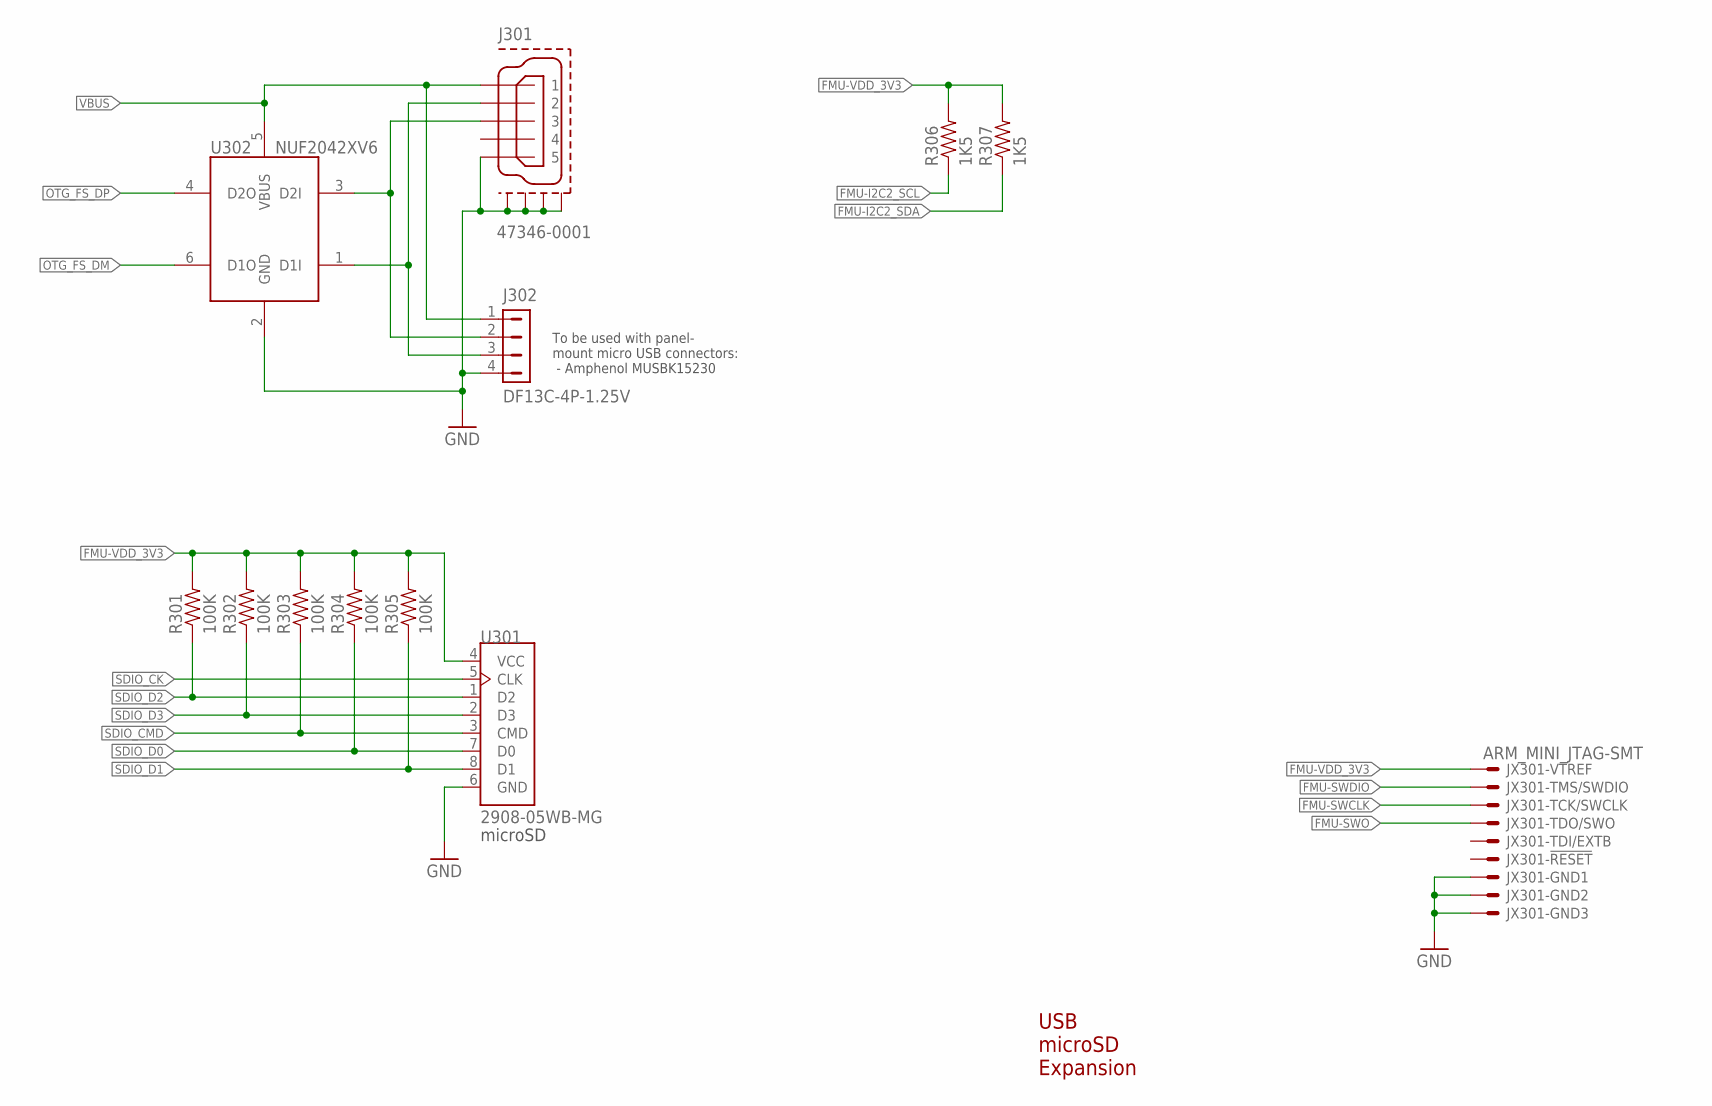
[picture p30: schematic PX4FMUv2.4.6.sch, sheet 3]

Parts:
J301: 47346-0001; MOLEX-47346-0001; PARTNO 47346-0001
J302: DF13C-4P-1.25V; PARTNO DF13C-4P-1.25V(20)
JX301: ARM_MINI_JTAG-SMT; FTSH-105-01-XXX-DV-K; PARTNO M50-3900542
R301, R302, R303, R304, R305: 100K; 0402-RES; PARTNO RC0402FR-07100KL
R306, R307: 1K5; 0402-RES; PARTNO RC0402FR-071K5L
U301: 2908-05WB-MG; MICROSD; PARTNO 2908-05WB-MG
U302: NUF2042XV6; SOT563-6; PARTNO NUF2042XV6T1G

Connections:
FMU-I2C2_SCL: R306.P$1 (1); also elsewhere on the board
FMU-I2C2_SDA: R307.P$1 (1); also elsewhere on the board
FMU-SWCLK: JX301.4; also elsewhere on the board
FMU-SWDIO: JX301.2; also elsewhere on the board
FMU-SWO: JX301.6; also elsewhere on the board
FMU-VDD_3V3: JX301.1, R301.P$2 (2), R302.P$2 (2), R303.P$2 (2), R304.P$2 (2), R305.P$2 (2), R306.P$2 (2), R307.P$2 (2), U301.4 (VCC); also elsewhere on the board
GND: J301.GND (5), J301.GND1, J301.GND2, J301.GND3, J301.GND4, J302.4, JX301.3, JX301.5, JX301.9, U301.6 (GND), U302.2 (GND); also elsewhere on the board
OTG_DM1: J301.D- (2), J302.3, U302.1 (D1I)
OTG_DP1: J301.D+ (3), J302.2, U302.3 (D2I)
OTG_FS_DM: U302.6 (D1O); also elsewhere on the board
OTG_FS_DP: U302.4 (D2O); also elsewhere on the board
SDIO_CK: U301.5 (CLK); also elsewhere on the board
SDIO_CMD: R303.P$1 (1), U301.3 (CMD); also elsewhere on the board
SDIO_D0: R304.P$1 (1), U301.7 (D0); also elsewhere on the board
SDIO_D1: R305.P$1 (1), U301.8 (D1); also elsewhere on the board
SDIO_D2: R301.P$1 (1), U301.1 (D2); also elsewhere on the board
SDIO_D3: R302.P$1 (1), U301.2 (D3); also elsewhere on the board
VBUS: J301.VBUS (1), J302.1, U302.5 (VBUS); also elsewhere on the board

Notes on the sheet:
USB microSD Expansion
microSD
To be used with panel- mount micro USB connectors: - Amphenol MUSBK15230

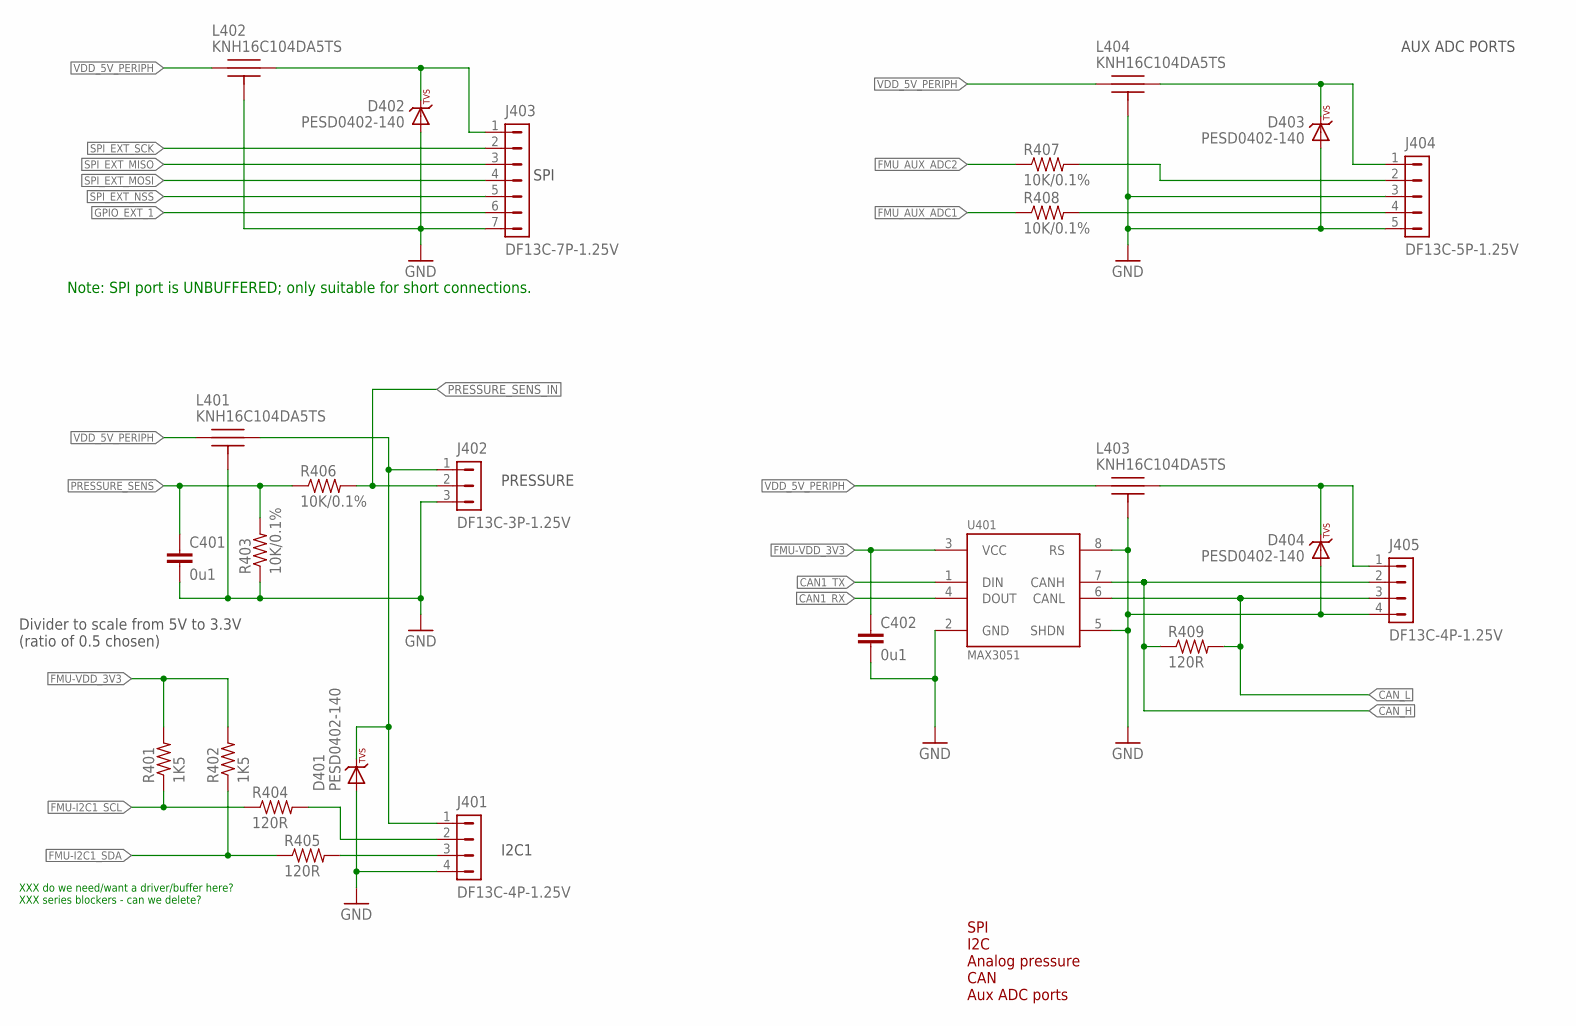
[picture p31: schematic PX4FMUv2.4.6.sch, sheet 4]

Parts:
C401, C402: 0u1; 0402-CAP; PARTNO CC0402ZRY5V7BB104
D401, D402, D403, D404: PESD0402-140; 0402-TVS; PARTNO PESD0402-140
J401, J405: DF13C-4P-1.25V; PARTNO DF13C-4P-1.25V(20)
J402: DF13C-3P-1.25V; PARTNO DF13C-3P-1.25V(20)
J403: DF13C-7P-1.25V; PARTNO DF13C-7P-1.25V(20)
J404: DF13C-5P-1.25V; PARTNO DF13C-5P-1.25V(20)
L401, L402, L403, L404: KNH16C104DA5TS; KYOCERA-KNH16-DA; PARTNO KNH16C104DA5TS
R401, R402: 1K5; 0402-RES; PARTNO RC0402FR-071K5L
R403, R406, R407, R408: 10K/0.1%; 0402-RES; PARTNO ERA-2AEB103X
R404, R405, R409: 120R; 0402-RES; PARTNO RC0402FR-07120RL
U401: MAX3051; SOT23-8; PARTNO MAX3051EKA

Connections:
!SPI_EXT_NSS: J403.5; also elsewhere on the board
CAN1_RX: U401.4 (DOUT); also elsewhere on the board
CAN1_TX: U401.1 (DIN); also elsewhere on the board
CAN_H: J405.2, R409.P$1 (1), U401.7 (CANH); also elsewhere on the board
CAN_L: J405.3, R409.P$2 (2), U401.6 (CANL); also elsewhere on the board
FMU-I2C1_SCL: R401.P$1 (1), R404.P$1 (1); also elsewhere on the board
FMU-I2C1_SDA: R402.P$1 (1), R405.P$1 (1); also elsewhere on the board
FMU-VDD_3V3: C402.P$1 (1), R401.P$2 (2), R402.P$2 (2), U401.3 (VCC); also elsewhere on the board
FMU_AUX_ADC1: R408.P$1 (1); also elsewhere on the board
FMU_AUX_ADC1_PROT: J404.4, R408.P$2 (2)
FMU_AUX_ADC2: R407.P$1 (1); also elsewhere on the board
FMU_AUX_ADC2_PROT: J404.2, R407.P$2 (2)
GND: C401.P$2 (2), C402.P$2 (2), D401.A, D402.A, D403.A, D404.A, J401.4, J402.3, J403.7, J404.3, J404.5, J405.4, L401.P$3, L401.P$4, L401.P$5, L402.P$3, L402.P$4, L402.P$5, L403.P$3, L403.P$4, L403.P$5, L404.P$3, L404.P$4, L404.P$5, R403.P$1 (1), U401.2 (GND), U401.5 (SHDN), U401.8 (RS); also elsewhere on the board
GPIO_EXT_1: J403.6; also elsewhere on the board
unnamed: J401.2, R404.P$2 (2)
unnamed: J401.3, R405.P$2 (2)
unnamed: D402.C, J403.1, L402.P$2
unnamed: D401.C, J401.1, J402.1, L401.P$2
unnamed: D404.C, J405.1, L403.P$2
unnamed: D403.C, J404.1, L404.P$2
PRESSURE_SENS: C401.P$1 (1), R403.P$2 (2), R406.P$1 (1); also elsewhere on the board
PRESSURE_SENS_IN: J402.2, R406.P$2 (2); also elsewhere on the board
SPI_EXT_MISO: J403.3; also elsewhere on the board
SPI_EXT_MOSI: J403.4; also elsewhere on the board
SPI_EXT_SCK: J403.2; also elsewhere on the board
VDD_5V_PERIPH: L401.P$1, L402.P$1, L403.P$1, L404.P$1; also elsewhere on the board

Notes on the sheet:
SPI
PRESSURE
XXX do we need/want a driver/buffer here? XXX series blockers - can we delete?
I2C1
AUX ADC PORTS
SPI I2C Analog pressure CAN Aux ADC ports
Note: SPI port is UNBUFFERED; only suitable for short connections.
Divider to scale from 5V to 3.3V (ratio of 0.5 chosen)

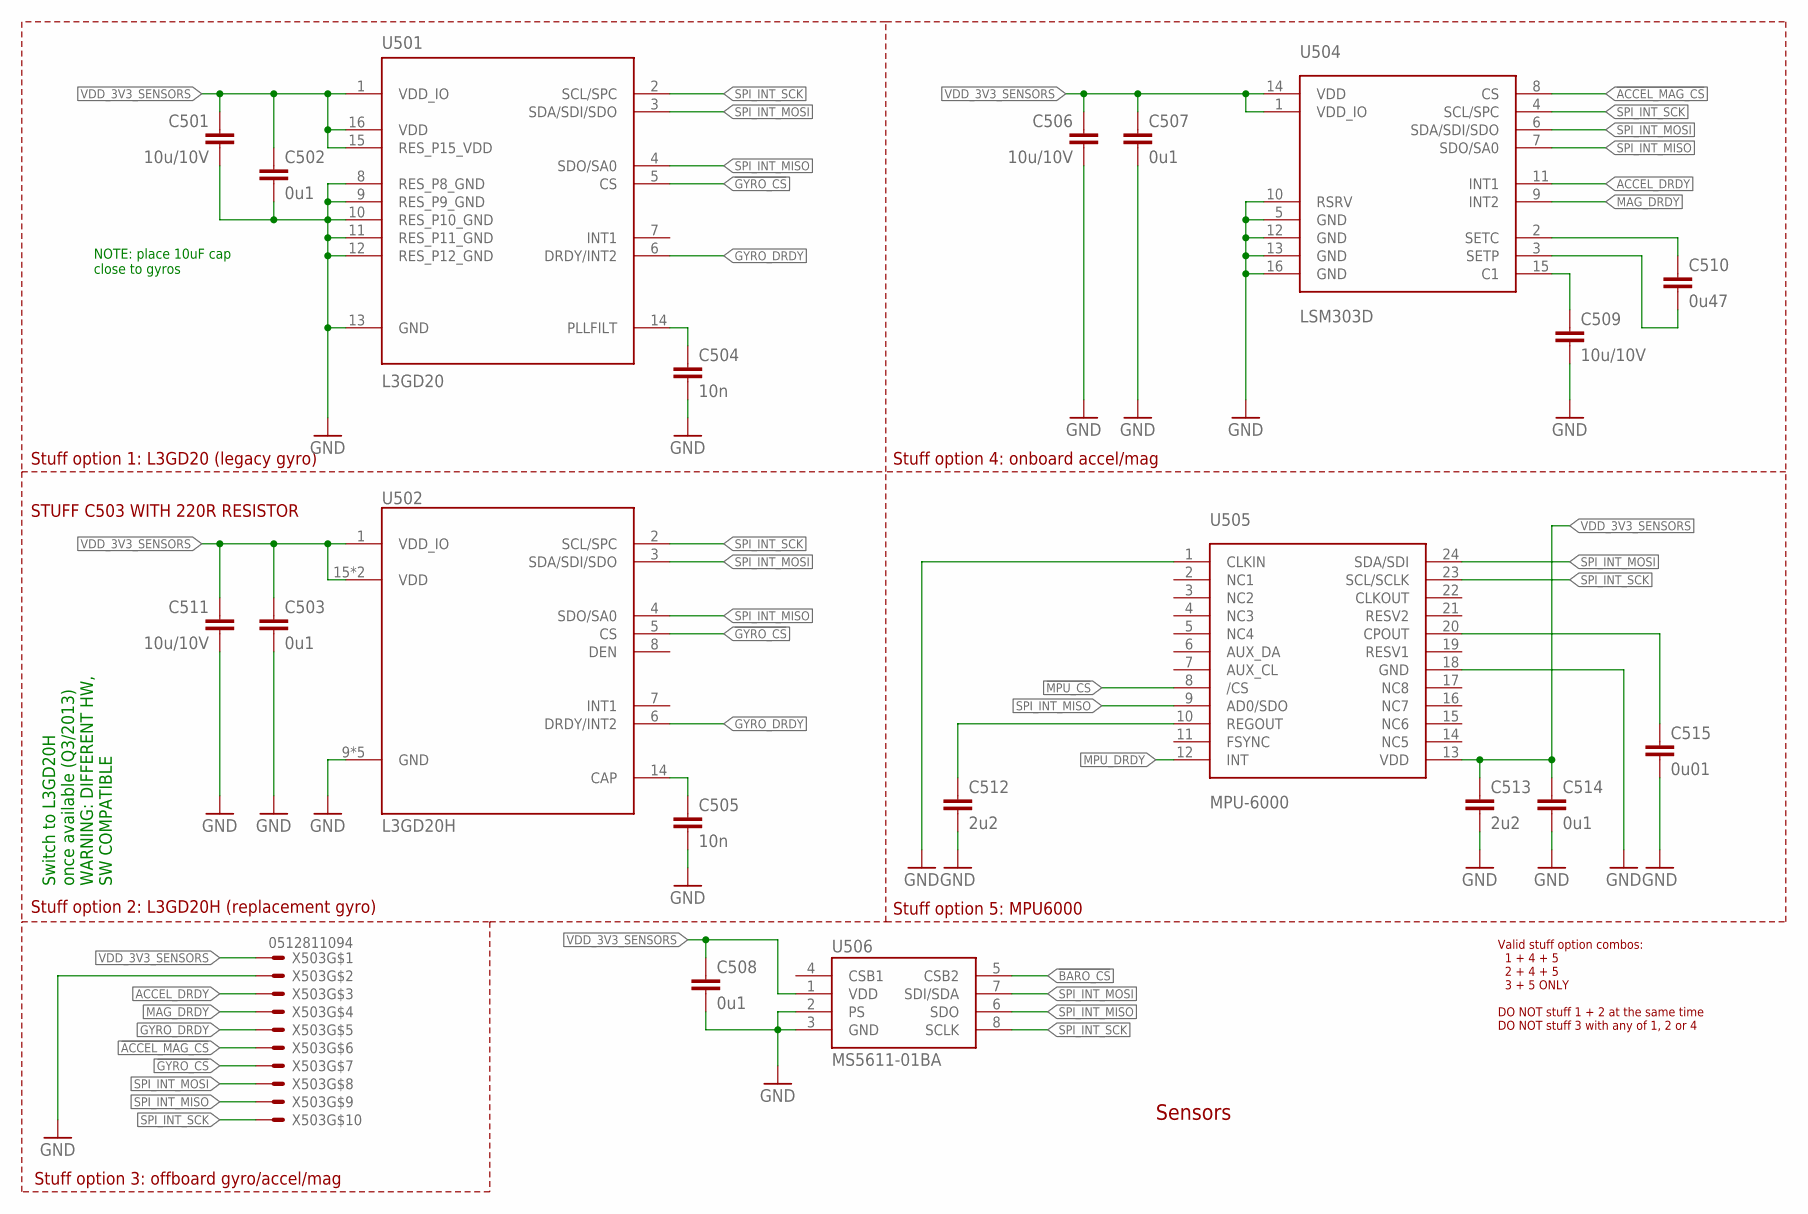
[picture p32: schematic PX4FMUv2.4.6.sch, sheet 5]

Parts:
C501, C506, C509, C511: 10u/10V; 0805-CAP; PARTNO CC0805ZKY5V6BB106
C502, C503, C507, C508, C514: 0u1; 0402-CAP; PARTNO CC0402ZRY5V7BB104
C504, C505: 10n; 0402-CAP; PARTNO CC0402KRX7R7BB103
C510: 0u47; 0402-CAP; PARTNO C1005X5R1C474K050BC
C512, C513: 2u2; 0603-CAP; PARTNO C1608X6S1C225K080AC
C515: 0u01; 0603-CAP; PARTNO 06033C103JAT2A
U501: L3GD20; L3G4200DH-MAN; PARTNO L3GD20
U502: L3GD20H; LGA-16L; PARTNO L3GD20H
U504: LSM303D; LGA-16L; PARTNO LSM303D
U505: MPU-6000; QFN-24; PARTNO MPU-6000
U506: MS5611-01BA; PARTNO MS5611-01BA
X503: 0512811094; 51281-1094; PARTNO 0781191109

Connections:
!ACCEL_MAG_CS: U504.8 (CS), X503.6; also elsewhere on the board
!BARO_CS: U506.5 (CSB2); also elsewhere on the board
!GYRO_CS: U501.5 (CS), U502.5 (CS), X503.7; also elsewhere on the board
!MPU_CS: U505.8 (/CS); also elsewhere on the board
ACCEL_DRDY: U504.11 (INT1), X503.3; also elsewhere on the board
GND: C501.P$2 (2), C502.P$2 (2), C503.P$2 (2), C504.P$2 (2), C505.P$2 (2), C506.P$2 (2), C507.P$2 (2), C508.P$2 (2), C509.P$2 (2), C511.P$2 (2), C512.P$2 (2), C513.P$2 (2), C514.P$2 (2), C515.P$2 (2), U501.8 (RES_P8_GND), U501.9 (RES_P9_GND), U501.10 (RES_P10_GND), U501.11 (RES_P11_GND), U501.12 (RES_P12_GND), U501.13 (GND), U502.9 (GND), U502.10 (GND), U502.11 (GND), U502.12 (GND), U502.13 (GND), U504.5 (GND), U504.10 (RSRV), U504.12 (GND), U504.13 (GND), U504.16 (GND), U505.1 (CLKIN), U505.18 (GND), U506.2 (PS), U506.3 (GND), X503.2; also elsewhere on the board
GYRO_DRDY: U501.6 (DRDY/INT2), U502.6 (DRDY/INT2), X503.5; also elsewhere on the board
MAG_DRDY: U504.9 (INT2), X503.4; also elsewhere on the board
MPU_DRDY: U505.12 (INT); also elsewhere on the board
unnamed: C509.P$1 (1), U504.15 (C1)
unnamed: C510.P$1 (1), U504.2 (SETC)
unnamed: C510.P$2 (2), U504.3 (SETP)
unnamed: C505.P$1 (1), U502.14 (CAP)
unnamed: C504.P$1 (1), U501.14 (PLLFILT)
unnamed: C512.P$1 (1), U505.10 (REGOUT)
unnamed: C515.P$1 (1), U505.20 (CPOUT)
SPI_INT_MISO: U501.4 (SDO/SA0), U502.4 (SDO/SA0), U504.7 (SDO/SA0), U505.9 (AD0/SDO), U506.6 (SDO), X503.9; also elsewhere on the board
SPI_INT_MOSI: U501.3 (SDA/SDI/SDO), U502.3 (SDA/SDI/SDO), U504.6 (SDA/SDI/SDO), U505.24 (SDA/SDI), U506.7 (SDI/SDA), X503.8; also elsewhere on the board
SPI_INT_SCK: U501.2 (SCL/SPC), U502.2 (SCL/SPC), U504.4 (SCL/SPC), U505.23 (SCL/SCLK), U506.8 (SCLK), X503.10; also elsewhere on the board
VDD_3V3_SENSORS: C501.P$1 (1), C502.P$1 (1), C503.P$1 (1), C506.P$1 (1), C507.P$1 (1), C508.P$1 (1), C511.P$1 (1), C513.P$1 (1), C514.P$1 (1), U501.1 (VDD_IO), U501.15 (RES_P15_VDD), U501.16 (VDD), U502.1 (VDD_IO), U502.15 (VDD), U502.16 (VDD), U504.1 (VDD_IO), U504.14 (VDD), U505.13 (VDD), U506.1 (VDD), X503.1; also elsewhere on the board

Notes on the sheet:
Sensors
Switch to L3GD20H once available (Q3/2013) WARNING: DIFFERENT HW, SW COMPATIBLE
NOTE: place 10uF cap close to gyros
Stuff option 1: L3GD20 (legacy gyro)
Stuff option 2: L3GD20H (replacement gyro)
Stuff option 4: onboard accel/mag
Valid stuff option combos: 1 + 4 + 5 2 + 4 + 5 3 + 5 ONLY DO NOT stuff 1 + 2 at the same time DO NOT stuff 3 with any of 1, 2 or 4
Stuff option 5: MPU6000
Stuff option 3: offboard gyro/accel/mag
STUFF C503 WITH 220R RESISTOR

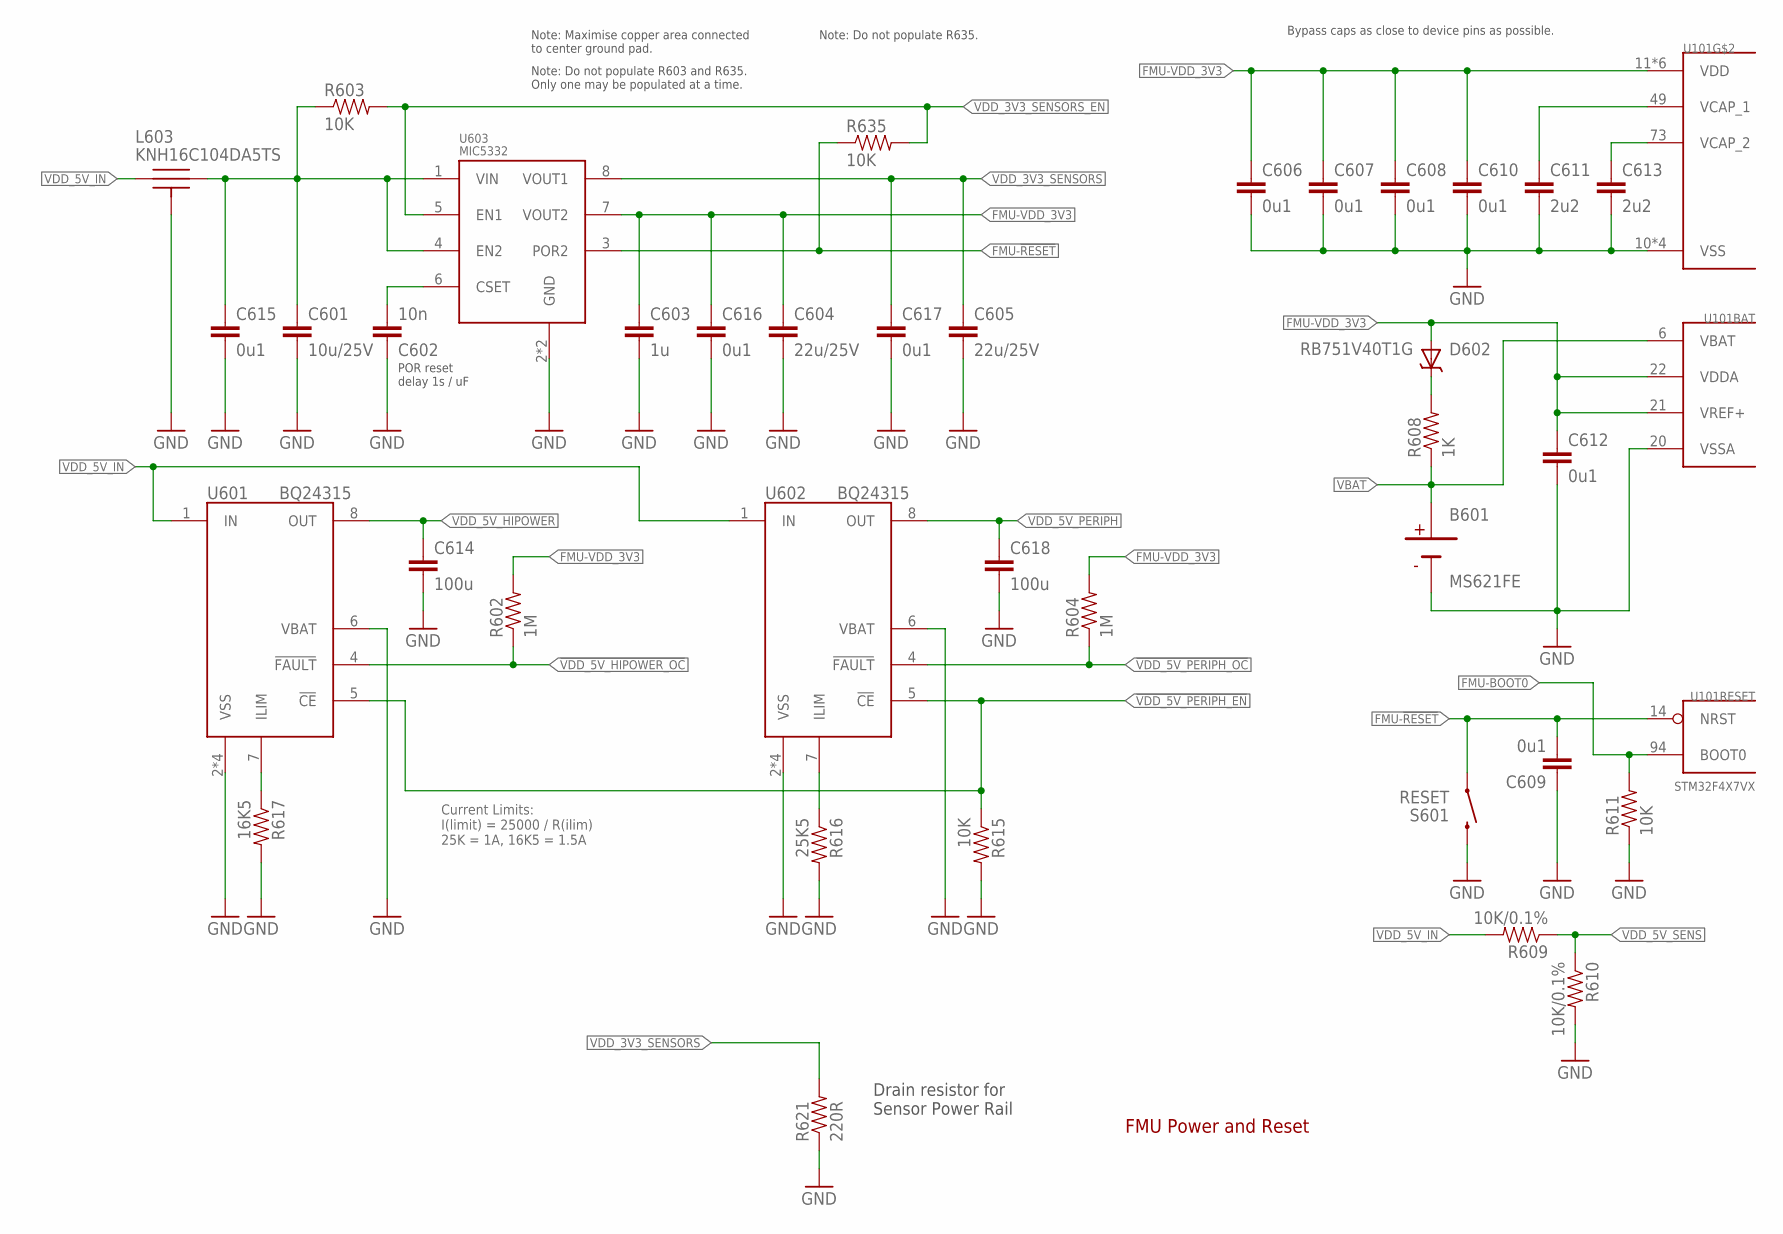
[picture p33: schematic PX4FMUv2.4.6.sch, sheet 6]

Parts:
B601: MS621FE; PARTNO MS621FE-FL11E
C601: 10u/25V; 0805-CAP; PARTNO CL21A106KAYNNNE
C602: 10n; 0402-CAP; PARTNO CC0402KRX7R7BB103
C603: 1u; 0603-CAP; PARTNO CC0603ZRY5V7BB105
C604, C605: 22u/25V; 0805-CAP; PARTNO CL21A226MAQNNNE
C606, C607, C608, C609, C610, C612, C615, C616, C617: 0u1; 0402-CAP; PARTNO CC0402ZRY5V7BB104
C611, C613: 2u2; 0603-CAP; PARTNO C1608X6S1C225K080AC
C614, C618: 100u; 1206-CAP; PARTNO C3216X5R1A107M160AC
D602: RB751V40T1G; SOD323; PARTNO RB751V40T1G
L603: KNH16C104DA5TS; KYOCERA-KNH16-DA; PARTNO KNH16C104DA5TS
R602, R604: 1M; 0402-RES; PARTNO RC0402FR-071ML
R603, R611, R615, R635: 10K; 0402-RES; PARTNO RC0402FR-0710KL
R608: 1K; 0402-RES; PARTNO RC0402FR-071KL
R609, R610: 10K/0.1%; 0402-RES; PARTNO ERA-2AEB103X
R616: 25K5; 0402-RES; PARTNO RMCF0402FT25K5
R617: 16K5; 0402-RES; PARTNO RMCF0402FT16K5
R621: 220R; 0603-RES; PARTNO RC1608J100CS
S601: RESET; EVQP7J01K; PARTNO EVQ-P7J01P
U101: STM32F4X7VX; TQFP100; PARTNO STM32F427VI
U601, U602: BQ24315; QFN8-DSG; PARTNO BQ24315DSGR
U603: MIC5332; MLF-8-EPAD; PARTNO MIC5332-SSYMT

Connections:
!VDD_5V_HIPOWER_OC: R602.P$1 (1), U601.4 (!FAULT); also elsewhere on the board
!VDD_5V_PERIPH_EN: R615.P$1 (1), U601.5 (!CE), U602.5 (!CE); also elsewhere on the board
!VDD_5V_PERIPH_OC: R604.P$1 (1), U602.4 (!FAULT); also elsewhere on the board
FMU-!RESET: C609.P$2 (2), R635.P$1 (1), S601.A1 (1), U101.14 (NRST), U603.3 (POR2); also elsewhere on the board
FMU-BOOT0: R611.P$2 (2), U101.94 (BOOT0); also elsewhere on the board
FMU-VDD_3V3: C603.P$1 (1), C604.P$1 (1), C606.P$1 (1), C607.P$1 (1), C608.P$1 (1), C610.P$1 (1), C612.P$1 (1), C616.P$1 (1), D602.A, R602.P$2 (2), R604.P$2 (2), U101.11 (VDD), U101.19 (VDD), U101.21 (VREF+), U101.22 (VDDA), U101.28 (VDD), U101.50 (VDD), U101.75 (VDD), U101.100 (VDD), U603.7 (VOUT2); also elsewhere on the board
FMU-VDD_5V5: C601.P$1 (1), C615.P$1 (1), L603.P$2, R603.P$1 (1), U603.1 (VIN), U603.4 (EN2)
GND: B601.2 (NEG), C601.P$2 (2), C602.P$1 (1), C603.P$2 (2), C604.P$2 (2), C605.P$2 (2), C606.P$2 (2), C607.P$2 (2), C608.P$2 (2), C609.P$1 (1), C610.P$2 (2), C611.P$2 (2), C612.P$2 (2), C613.P$2 (2), C614.P$2 (2), C615.P$2 (2), C616.P$2 (2), C617.P$2 (2), C618.P$2 (2), L603.P$3, L603.P$4, L603.P$5, R610.P$2 (2), R611.P$1 (1), R615.P$2 (2), R616.P$2 (2), R617.P$2 (2), R621.1, S601.B3 (2), U101.10 (VSS), U101.20 (VSSA), U101.27 (VSS), U101.74 (VSS), U101.99 (VSS), U601.2 (VSS), U601.6 (VBAT), U601.GND (VSS), U601.P$2 (VSS), U601.P$3 (VSS), U602.2 (VSS), U602.6 (VBAT), U602.GND (VSS), U602.P$2 (VSS), U602.P$3 (VSS), U603.2 (GND), U603.GND; also elsewhere on the board
unnamed: C613.P$1 (1), U101.73 (VCAP_2)
unnamed: C602.P$2 (2), U603.6 (CSET)
unnamed: C611.P$1 (1), U101.49 (VCAP_1)
unnamed: D602.C, R608.P$2 (2)
unnamed: R616.P$1 (1), U602.7 (ILIM)
unnamed: R617.P$1 (1), U601.7 (ILIM)
VBAT: B601.1 (POS), R608.P$1 (1), U101.6 (VBAT); also elsewhere on the board
VDD_3V3_SENSORS: C605.P$1 (1), C617.P$1 (1), R621.2, U603.8 (VOUT1); also elsewhere on the board
VDD_3V3_SENSORS_EN: R603.P$2 (2), R635.P$2 (2), U603.5 (EN1); also elsewhere on the board
VDD_5V_HIPOWER: C614.P$1 (1), U601.8 (OUT); also elsewhere on the board
VDD_5V_IN: L603.P$1, R609.P$2 (2), U601.1 (IN), U602.1 (IN); also elsewhere on the board
VDD_5V_PERIPH: C618.P$1 (1), U602.8 (OUT); also elsewhere on the board
VDD_5V_SENS: R609.P$1 (1), R610.P$1 (1); also elsewhere on the board

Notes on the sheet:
FMU Power and Reset
Bypass caps as close to device pins as possible.
Note: Maximise copper area connected to center ground pad.
POR reset delay 1s / uF
Current Limits: I(limit) = 25000 / R(ilim) 25K = 1A, 16K5 = 1.5A
Drain resistor for Sensor Power Rail
Note: Do not populate R603 and R635. Only one may be populated at a time.
Note: Do not populate R635.

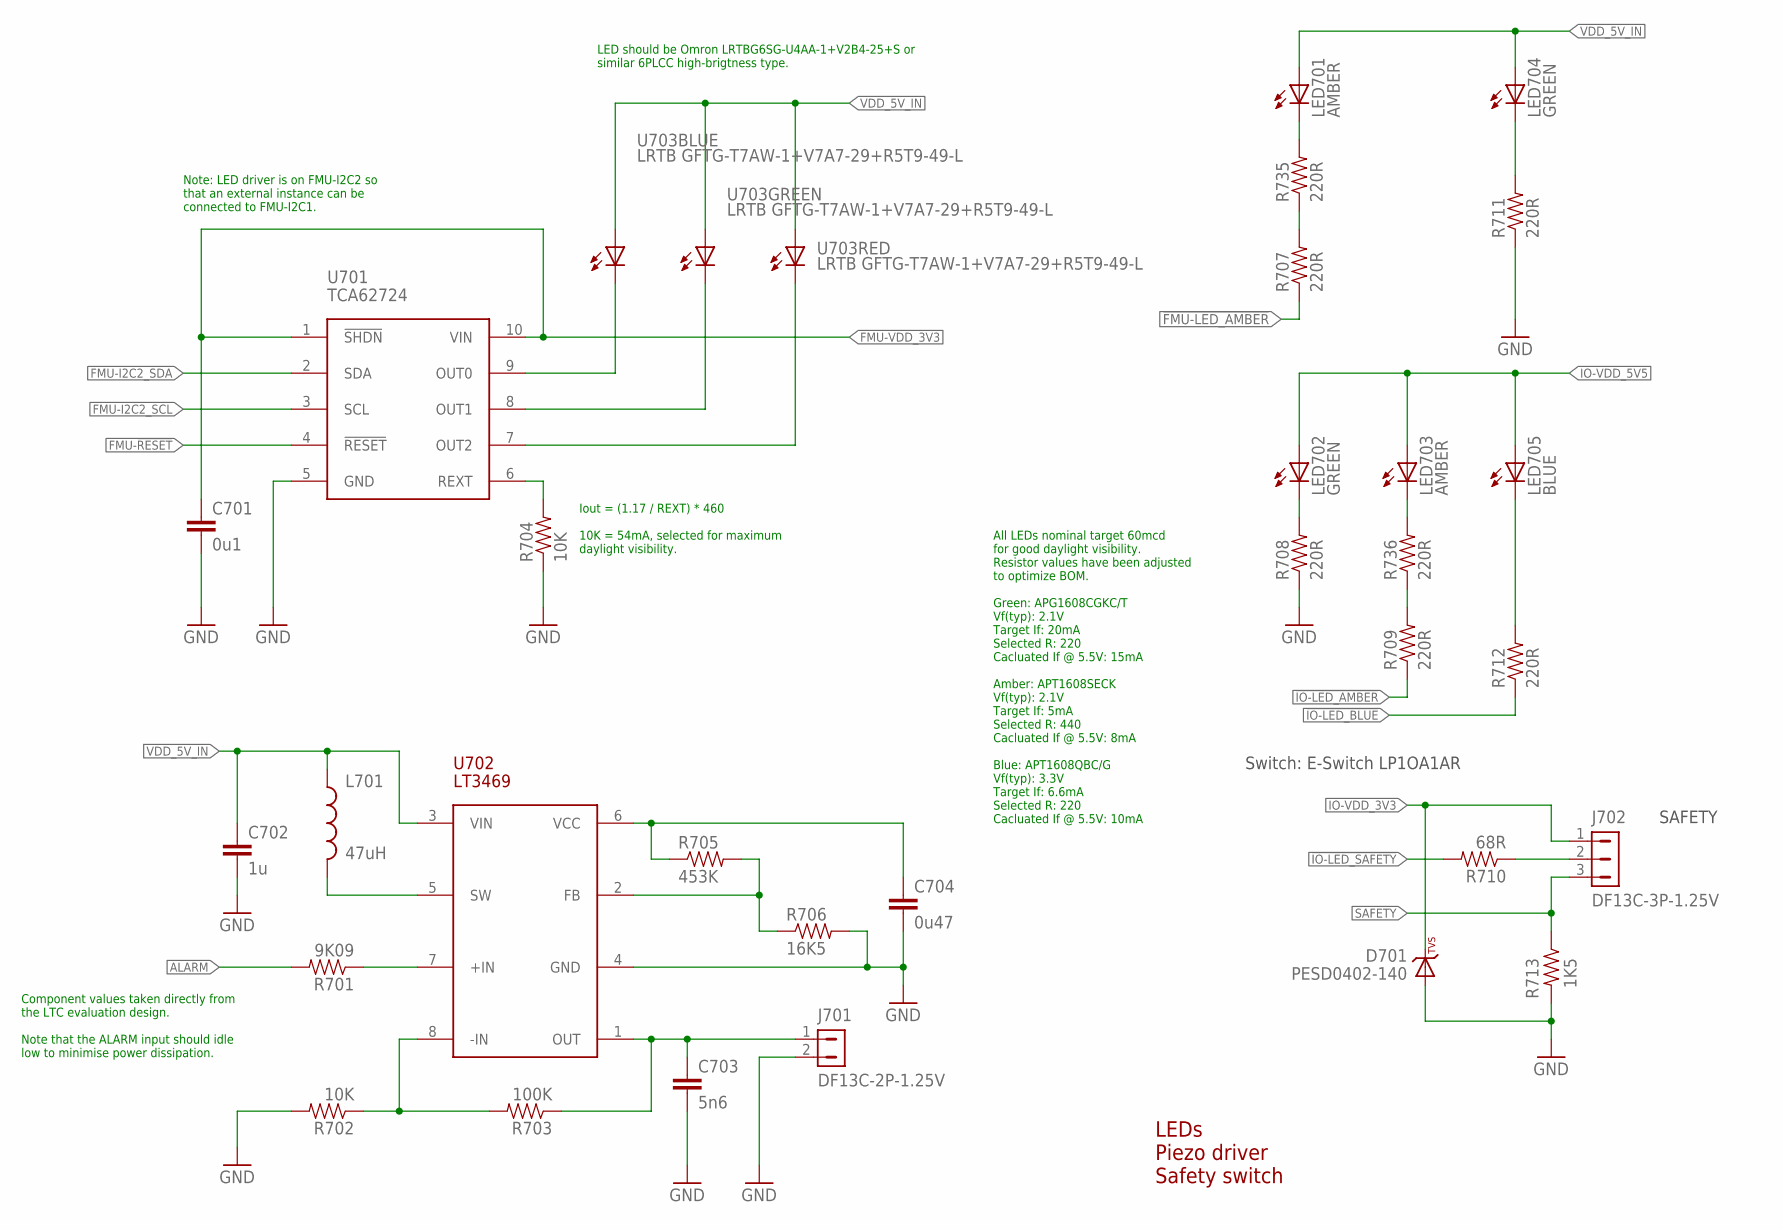
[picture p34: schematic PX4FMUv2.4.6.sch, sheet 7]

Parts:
C701: 0u1; 0402-CAP; PARTNO CC0402ZRY5V7BB104
C702: 1u; 0603-CAP; PARTNO CC0603ZRY5V7BB105
C703: 5n6; 0402-CAP; PARTNO C0402C562K5RACTU
C704: 0u47; 0402-CAP; PARTNO C1005X5R1C474K050BC
D701: PESD0402-140; 0402-TVS; PARTNO PESD0402-140
J701: DF13C-2P-1.25V; PARTNO DF13C-2P-1.25V(20)
J702: DF13C-3P-1.25V; PARTNO DF13C-3P-1.25V(20)
L701: 47uH; 0805-IND; PARTNO MLZ2012M470W
LED701, LED703: AMBER; 0603-LED; PARTNO APTD1608SECK
LED702, LED704: GREEN; 0603-LED; PARTNO APTD1608CGCK
LED705: BLUE; 0603-LED; PARTNO APTD1608QBC/D
R701: 9K09; 0402-RES; PARTNO RMCF0402FT9K09
R702, R704: 10K; 0402-RES; PARTNO RC0402FR-0710KL
R703: 100K; 0402-RES; PARTNO RC0402FR-07100KL
R705: 453K; 0402-RES; PARTNO RMCF0402FT453K
R706: 16K5; 0402-RES; PARTNO RMCF0402FT16K5
R707, R708, R709, R711, R712, R735, R736: 220R; 0402-RES; PARTNO RC0402FR-07220RL
R710: 68R; 0402-RES; PARTNO ERJ-2GEJ680X
R713: 1K5; 0402-RES; PARTNO RC0402FR-071K5L
U701: TCA62724FMG; SON10; PARTNO TCA62724FMG
U702: LT3469; SOT23-8; PARTNO LT3469ETS8
U703: LRTB GFTG-T7AW-1+V7A7-29+R5T9-49-L; 6-PLCC; PARTNO LRTB GFTG-T7AW-1+V7A7-29+R5T9-49-L

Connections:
!FMU-LED_AMBER: R707.P$1 (1); also elsewhere on the board
!IO-LED_AMBER: R709.P$1 (1); also elsewhere on the board
!IO-LED_BLUE: R712.P$1 (1); also elsewhere on the board
!IO-LED_SAFETY: R710.P$2 (2); also elsewhere on the board
ALARM: R701.P$2 (2); also elsewhere on the board
FMU-!RESET: U701.4 (!RESET); also elsewhere on the board
FMU-I2C2_SCL: U701.3 (SCL); also elsewhere on the board
FMU-I2C2_SDA: U701.2 (SDA); also elsewhere on the board
FMU-VDD_3V3: C701.P$1 (1), U701.1 (!SHDN), U701.10 (VIN); also elsewhere on the board
GND: C701.P$2 (2), C702.P$2 (2), C703.P$2 (2), C704.P$2 (2), D701.A, J701.2, R702.P$2 (2), R704.P$1 (1), R706.P$2 (2), R708.P$1 (1), R711.P$1 (1), R713.P$2 (2), U701.5 (GND), U702.4 (GND); also elsewhere on the board
IO-VDD_3V3: D701.C, J702.1; also elsewhere on the board
IO-VDD_5V5: LED702.A, LED703.A, LED705.A; also elsewhere on the board
unnamed: LED704.C, R711.P$2 (2)
unnamed: LED705.C, R712.P$2 (2)
unnamed: R707.P$2 (2), R735.P$1 (1)
unnamed: R705.P$2 (2), R706.P$1 (1), U702.2 (FB)
unnamed: R702.P$1 (1), R703.P$2 (2), U702.8 (-IN)
unnamed: LED701.C, R735.P$2 (2)
unnamed: C703.P$1 (1), J701.1, R703.P$1 (1), U702.1 (OUT)
unnamed: R701.P$1 (1), U702.7 (+IN)
unnamed: LED702.C, R708.P$2 (2)
unnamed: L701.P$2 (2), U702.5 (SW)
unnamed: C704.P$1 (1), R705.P$1 (1), U702.6 (VCC)
unnamed: R709.P$2 (2), R736.P$1 (1)
unnamed: LED703.C, R736.P$2 (2)
unnamed: J702.2, R710.P$1 (1)
unnamed: R704.P$2 (2), U701.6 (REXT)
RGB_LED_3: U701.9 (OUT0), U703.C1 (C)
RGB_LED_4: U701.8 (OUT1), U703.C2 (C)
RGB_LED_14: U701.7 (OUT2), U703.C3 (C)
SAFETY: J702.3, R713.P$1 (1); also elsewhere on the board
VDD_5V_IN: C702.P$1 (1), L701.P$1 (1), LED701.A, LED704.A, U702.3 (VIN), U703.A1 (A), U703.A2 (A), U703.A3 (A); also elsewhere on the board

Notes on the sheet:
LEDs Piezo driver Safety switch
Switch: E-Switch LP1OA1AR
SAFETY
LED should be Omron LRTBG6SG-U4AA-1+V2B4-25+S or similar 6PLCC high-brigtness type.
Iout = (1.17 / REXT) * 460 10K = 54mA, selected for maximum daylight visibility.
Note: LED driver is on FMU-I2C2 so that an external instance can be connected to FMU-I2C1.
All LEDs nominal target 60mcd for good daylight visibility. Resistor values have been adjusted to optimize BOM. Green: APG1608CGKC/T Vf(typ): 2.1V Target If: 20mA Selected R: 220 Cacluated If @ 5.5V: 15mA Amber: APT1608SECK Vf(typ): 2.1V Target If: 5mA Selected R: 440 Cacluated If @ 5.5V: 8mA Blue: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
Component values taken directly from the LTC evaluation design. Note that the ALARM input should idle low to minimise power dissipation.

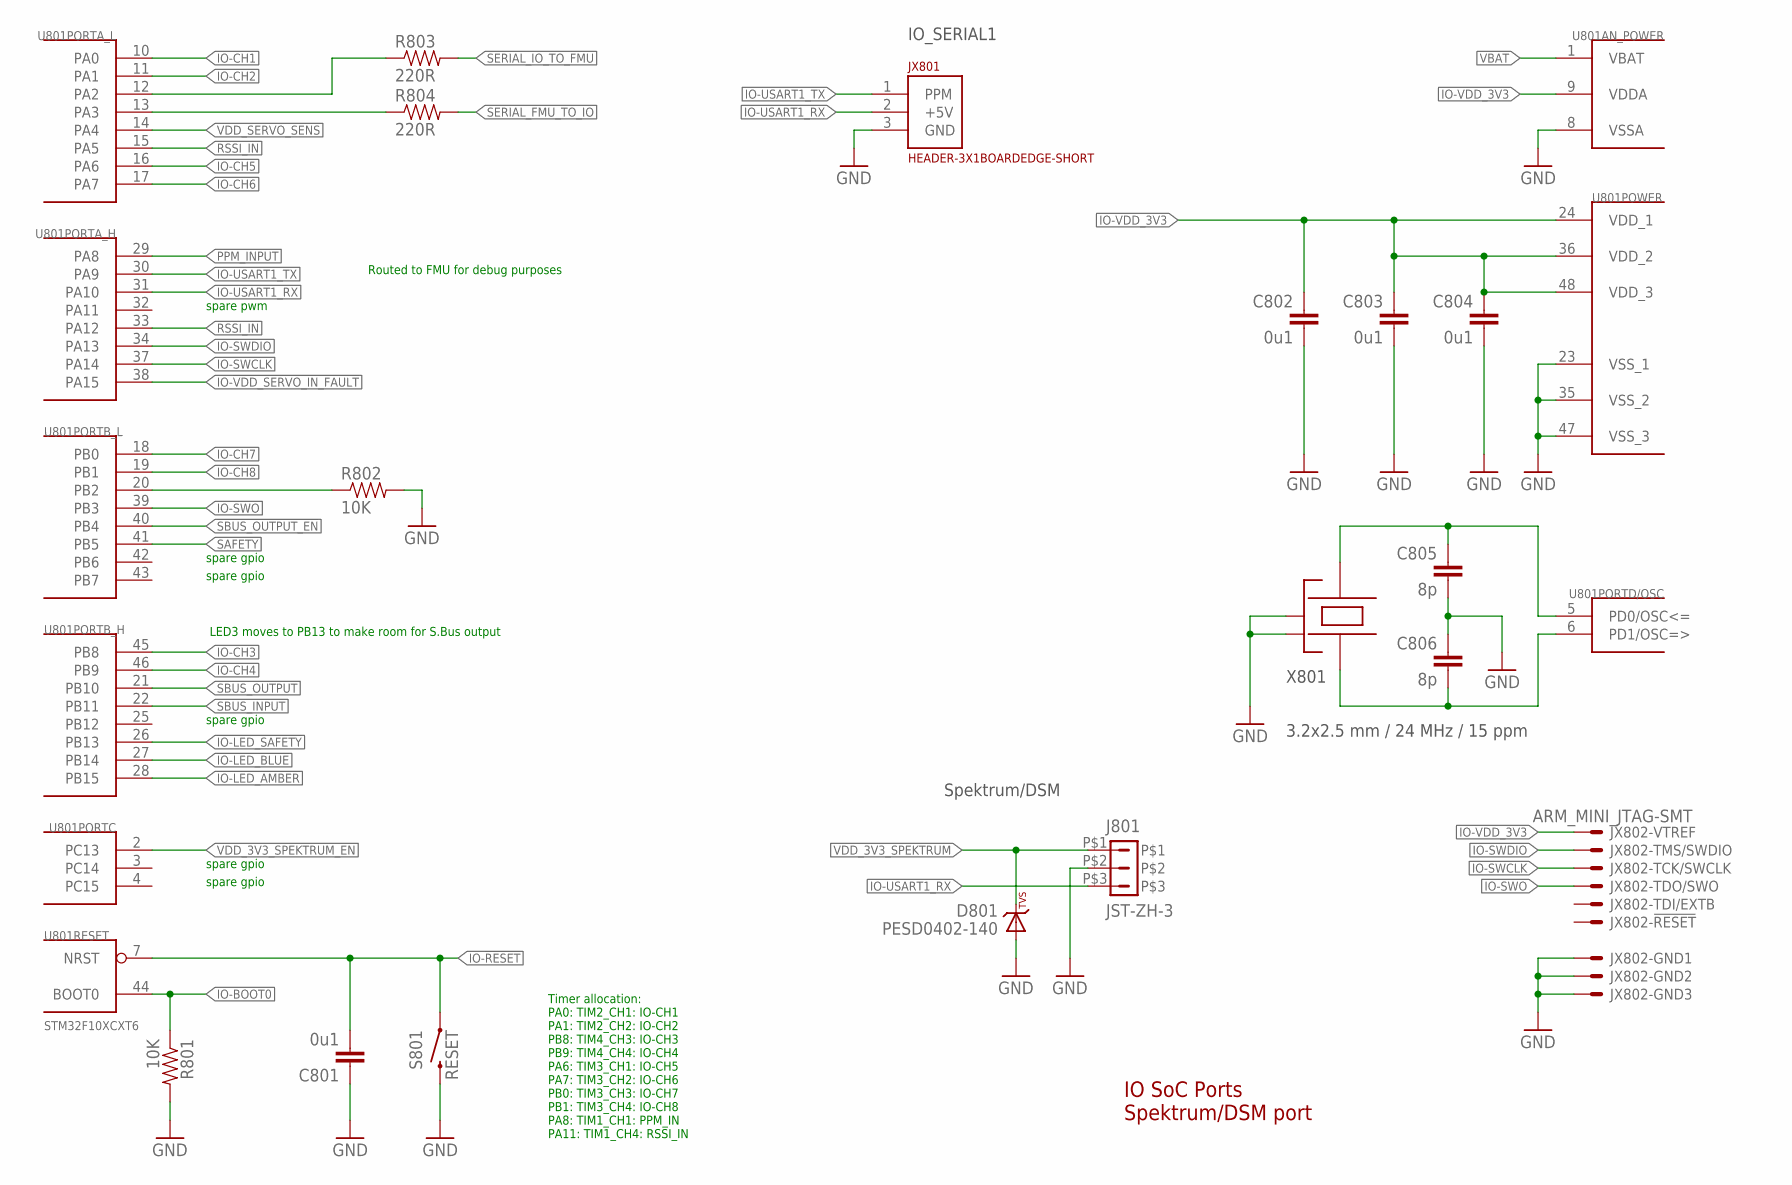
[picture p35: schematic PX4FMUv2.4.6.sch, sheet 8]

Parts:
C801, C802, C803, C804: 0u1; 0402-CAP; PARTNO CC0402ZRY5V7BB104
C805, C806: 8p; 0402-CAP; PARTNO C1005C0G1H080C
D801: PESD0402-140; 0402-TVS; PARTNO PESD0402-140
J801: JST-ZH-3; JST-ZH-SMT-VERTICAL; PARTNO B3B-ZR-SM4-TF (LF)(SN)(P)
JX801: HEADER-3X1BOARDEDGE-SHORT; HEADER_3X01_SMD_H_BOARD_EDGE_SHORT
JX802: ARM_MINI_JTAG-SMT; FTSH-105-01-XXX-DV-K; PARTNO M50-3900542
R801, R802: 10K; 0402-RES; PARTNO RC0402FR-0710KL
R803, R804: 220R; 0402-RES; PARTNO RC0402FR-07220RL
S801: RESET; EVQP7J01K; PARTNO EVQ-P7J01P
U801: STM32F10XCXT6; TQFP48; PARTNO STM32F100C8T6B
X801: 3.2x2.5 mm / 24 MHz / 15 ppm; OSCILLATOR-3.2X2.5; PARTNO NX3225SA-24.000000MHZ

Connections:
!IO-LED_AMBER: U801.28 (PB15); also elsewhere on the board
!IO-LED_BLUE: U801.27 (PB14); also elsewhere on the board
!IO-LED_SAFETY: U801.26 (PB13); also elsewhere on the board
!SBUS_OUTPUT_EN: U801.40 (PB4); also elsewhere on the board
GND: C801.P$1 (1), C802.P$2 (2), C803.P$2 (2), C804.P$2 (2), C805.P$2 (2), C806.P$1 (1), D801.A, J801.P$2, JX801.3 (GND), JX802.3, JX802.5, JX802.9, R801.P$2 (2), R802.P$2 (2), S801.B3 (2), U801.8 (VSSA), U801.23 (VSS_1), U801.35 (VSS_2), U801.47 (VSS_3), X801.2 (NC_2), X801.4 (NC_4); also elsewhere on the board
IO-!RESET: C801.P$2 (2), S801.A1 (1), U801.7 (NRST); also elsewhere on the board
IO-!VDD_SERVO_IN_FAULT: U801.38 (PA15); also elsewhere on the board
IO-BOOT0: R801.P$1 (1), U801.44 (BOOT0); also elsewhere on the board
IO-BOOT1: R802.P$1 (1), U801.20 (PB2)
IO-CH1: U801.10 (PA0); also elsewhere on the board
IO-CH2: U801.11 (PA1); also elsewhere on the board
IO-CH3: U801.45 (PB8); also elsewhere on the board
IO-CH4: U801.46 (PB9); also elsewhere on the board
IO-CH5: U801.16 (PA6); also elsewhere on the board
IO-CH6: U801.17 (PA7); also elsewhere on the board
IO-CH7: U801.18 (PB0); also elsewhere on the board
IO-CH8: U801.19 (PB1); also elsewhere on the board
IO-SWCLK: JX802.4, U801.37 (PA14)
IO-SWDIO: JX802.2, U801.34 (PA13)
IO-SWO: JX802.6, U801.39 (PB3)
IO-USART1_RX: J801.P$3, JX801.2 (+5V), U801.31 (PA10)
IO-USART1_TX: JX801.1 (PPM), U801.30 (PA9); also elsewhere on the board
IO-VDD_3V3: C802.P$1 (1), C803.P$1 (1), C804.P$1 (1), JX802.1, U801.9 (VDDA), U801.24 (VDD_1), U801.36 (VDD_2), U801.48 (VDD_3); also elsewhere on the board
unnamed: R803.P$1 (1), U801.12 (PA2)
unnamed: R804.P$1 (1), U801.13 (PA3)
unnamed: C806.P$2 (2), U801.6 (PD1/OSC=>), X801.1
unnamed: C805.P$1 (1), U801.5 (PD0/OSC<=), X801.3
PPM_INPUT: U801.29 (PA8); also elsewhere on the board
RSSI_IN: U801.15 (PA5), U801.33 (PA12); also elsewhere on the board
SAFETY: U801.41 (PB5); also elsewhere on the board
SBUS_INPUT: U801.22 (PB11); also elsewhere on the board
SBUS_OUTPUT: U801.21 (PB10); also elsewhere on the board
SERIAL_FMU_TO_IO: R804.P$2 (2); also elsewhere on the board
SERIAL_IO_TO_FMU: R803.P$2 (2); also elsewhere on the board
VBAT: U801.1 (VBAT); also elsewhere on the board
VDD_3V3_SPEKTRUM: D801.C, J801.P$1; also elsewhere on the board
VDD_3V3_SPEKTRUM_EN: U801.2 (PC13); also elsewhere on the board
VDD_SERVO_SENS: U801.14 (PA4); also elsewhere on the board

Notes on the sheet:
IO SoC Ports Spektrum/DSM port
LED3 moves to PB13 to make room for S.Bus output
Routed to FMU for debug purposes
IO_SERIAL1
Spektrum/DSM
Timer allocation: PA0: TIM2_CH1: IO-CH1 PA1: TIM2_CH2: IO-CH2 PB8: TIM4_CH3: IO-CH3 PB9: TIM4_CH4: IO-CH4 PA6: TIM3_CH1: IO-CH5 PA7: TIM3_CH2: IO-CH6 PB0: TIM3_CH3: IO-CH7 PB1: TIM3_CH4: IO-CH8 PA8: TIM1_CH1: PPM_IN PA11: TIM1_CH4: RSSI_IN
spare pwm
spare gpio

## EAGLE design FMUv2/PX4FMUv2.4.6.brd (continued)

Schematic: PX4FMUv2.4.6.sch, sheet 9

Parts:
C901, C902, C903: 0u1; 0402-CAP; PARTNO CC0402ZRY5V7BB104
D901, D902, D903: PESD0402-140; 0402-TVS; PARTNO PESD0402-140
D904: MSS1P4-M3; MICROSMP; PARTNO MSS1P4-M3/89A
J901: HEADER-3X163X16RA; 3X16RA
L901: KNH16C104DA5TS; KYOCERA-KNH16-DA; PARTNO KNH16C104DA5TS
R901: 10K; 0402-RES; PARTNO RC0402FR-0710KL
R902, R903, R904, R905, R906, R907, R908, R909, R910, R911, R912, R913, R914, R915, R916, R917: 220R; 0402-RES; PARTNO RC0402FR-07220RL
R918, R919, R922: 10K/0.1%; 0402-RES; PARTNO ERA-2AEB103X
U901, U902: TXS0108QFN20; QFN20-RGY; PARTNO TXS0108ERGYR
U903: 74LVC2G240; TSSOP8_SOT505-2; PARTNO 74LVC2G240DP,125

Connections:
!SBUS_OUTPUT_EN: U903.7 (!2OE); also elsewhere on the board
FMU-CH1: U901.7 (A6); also elsewhere on the board
FMU-CH1-PROT: J901.46, R913.P$2 (2)
FMU-CH2: U901.6 (A5); also elsewhere on the board
FMU-CH3: U901.5 (A4); also elsewhere on the board
FMU-CH4: U901.4 (A3); also elsewhere on the board
FMU-CH5: U901.3 (A2); also elsewhere on the board
FMU-CH6: U901.1 (A1); also elsewhere on the board
FMU-CH6-PROT: J901.31, R902.P$2 (2)
FMU-VDD_3V3: C902.P$1 (1), U901.2 (VCCA), U901.10 (OE), U901.19 (VCCB); also elsewhere on the board
GND: C901.P$2 (2), C902.P$2 (2), C903.P$2 (2), D901.A, D902.A, D903.A, J901.3, J901.6, J901.9, J901.12, J901.15, J901.18, J901.21, J901.24, J901.27, J901.30, J901.33, J901.36, J901.39, J901.42, J901.45, J901.48, L901.P$3, L901.P$4, L901.P$5, R919.P$1 (1), U901.11 (GND), U902.11 (GND), U903.1 (!1OE), U903.4 (GND); also elsewhere on the board
IO-CH1: U902.9 (A8); also elsewhere on the board
IO-CH1-PROT: J901.28, R917.P$2 (2)
IO-CH2: U902.8 (A7); also elsewhere on the board
IO-CH3: U902.7 (A6); also elsewhere on the board
IO-CH4: U902.6 (A5); also elsewhere on the board
IO-CH5: U902.5 (A4); also elsewhere on the board
IO-CH6: U902.4 (A3); also elsewhere on the board
IO-CH7: U902.3 (A2); also elsewhere on the board
IO-CH8: U902.1 (A1); also elsewhere on the board
IO-CH8-PROT: J901.7, R905.P$2 (2)
IO-VDD_3V3: C901.P$1 (1), C903.P$1 (1), U902.2 (VCCA), U902.10 (OE), U902.19 (VCCB), U903.8 (VCC); also elsewhere on the board
IO-VDD_5V5: J901.2; also elsewhere on the board
unnamed: R918.P$2 (2), R922.P$1 (1)
unnamed: J901.10, R914.P$2 (2)
unnamed: D902.C, R901.P$2 (2), R910.P$1 (1), U903.3 (2Y)
unnamed: R905.P$1 (1), U902.20 (B1)
unnamed: R914.P$1 (1), U902.18 (B2)
unnamed: R906.P$1 (1), U902.17 (B3)
unnamed: R915.P$1 (1), U902.16 (B4)
unnamed: R907.P$1 (1), U902.15 (B5)
unnamed: R916.P$1 (1), U902.14 (B6)
unnamed: R908.P$1 (1), U902.13 (B7)
unnamed: R917.P$1 (1), U902.12 (B8)
unnamed: R902.P$1 (1), U901.20 (B1)
unnamed: R911.P$1 (1), U901.18 (B2)
unnamed: R903.P$1 (1), U901.17 (B3)
unnamed: R912.P$1 (1), U901.16 (B4)
unnamed: R904.P$1 (1), U901.15 (B5)
unnamed: R913.P$1 (1), U901.14 (B6)
unnamed: J901.34, R911.P$2 (2)
unnamed: J901.13, R906.P$2 (2)
unnamed: J901.16, R915.P$2 (2)
unnamed: J901.19, R907.P$2 (2)
unnamed: J901.22, R916.P$2 (2)
unnamed: J901.25, R908.P$2 (2)
unnamed: J901.37, R903.P$2 (2)
unnamed: J901.40, R912.P$2 (2)
unnamed: J901.43, R904.P$2 (2)
unnamed: J901.4, R910.P$2 (2)
unnamed: D903.C, D904.CATHODE (C), L901.P$1
PPM-SBUS-PROT: J901.1, R909.P$2 (2)
PPM_INPUT: D901.C, R909.P$1 (1), U903.2 (1A); also elsewhere on the board
RSSI_IN: R901.P$1 (1); also elsewhere on the board
SBUS_INPUT: U903.6 (1Y); also elsewhere on the board
SBUS_OUTPUT: U903.5 (2A); also elsewhere on the board
VDD_SERVO: D904.ANODE (A), J901.5, J901.8, J901.11, J901.14, J901.17, J901.20, J901.23, J901.26, J901.29, J901.32, J901.35, J901.38, J901.41, J901.44, J901.47, R922.P$2 (2); also elsewhere on the board
VDD_SERVO_IN: L901.P$2; also elsewhere on the board
VDD_SERVO_SENS: R918.P$1 (1), R919.P$2 (2); also elsewhere on the board

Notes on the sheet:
Servo Header S.Bus interface
S.Bus in/out
Servo outputs

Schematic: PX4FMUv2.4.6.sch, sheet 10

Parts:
C1001: 10u/25V; 0805-CAP; PARTNO CL21A106KAYNNNE
C1002: 10n; 0402-CAP; PARTNO CC0402KRX7R7BB103
C1003: 1u; 0603-CAP; PARTNO CC0603ZRY5V7BB105
C1004: 10u; 0603-CAP; PARTNO C1608X5R1A106K080AC
C1005: 0u1; 0402-CAP; PARTNO CC0402ZRY5V7BB104
C1008: 2u2; 0402-CAP; PARTNO C1005X6S1C225K050BC
D1001: PMEG2005CT; SOT23-3; PARTNO PMEG2005CT
F1001: 0ZCA0035FF2G; PTC-1206; PARTNO 0ZCA0035FF2G
R1001: 100K; 0402-RES; PARTNO RC0402FR-07100KL
R1002: 10K; 0402-RES; PARTNO RC0402FR-0710KL
U1001: BQ24313; QFN8-DSG; PARTNO BQ24313DSGT
U1002: MIC5332; MLF-8-EPAD; PARTNO MIC5332-SSYMT

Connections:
GND: C1001.P$2 (2), C1002.P$2 (2), C1003.P$2 (2), C1004.P$2 (2), C1005.P$2 (2), C1008.P$2 (2), R1001.P$1 (1), R1002.P$1 (1), U1001.2 (VSS), U1001.5 (!CE), U1001.6 (VBAT), U1001.GND (VSS), U1001.P$2 (VSS), U1001.P$3 (VSS), U1002.2 (GND), U1002.GND; also elsewhere on the board
IO-!RESET: U1002.3 (POR2); also elsewhere on the board
IO-!VDD_SERVO_IN_FAULT: U1001.4 (!FAULT); also elsewhere on the board
IO-VDD_3V3: C1003.P$1 (1), C1004.P$1 (1), U1002.7 (VOUT2); also elsewhere on the board
IO-VDD_5V5: C1001.P$1 (1), C1005.P$1 (1), D1001.3 (CC), U1002.1 (VIN), U1002.4 (EN2); also elsewhere on the board
unnamed: D1001.2 (A2), U1001.8 (OUT)
unnamed: R1001.P$2 (2), U1001.7 (ILIM)
unnamed: D1001.1 (A1), F1001.2
unnamed: C1002.P$1 (1), U1002.6 (CSET)
VDD_3V3_SPEKTRUM: C1008.P$1 (1), U1002.8 (VOUT1); also elsewhere on the board
VDD_3V3_SPEKTRUM_EN: R1002.P$2 (2), U1002.5 (EN1); also elsewhere on the board
VDD_5V_IN: F1001.1; also elsewhere on the board
VDD_SERVO_IN: U1001.1 (IN); also elsewhere on the board

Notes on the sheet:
Dual supply from servo rail and FMU 5V rail
Current limit = 25 / Rilim (current in A, R in kOhms) 100K = 250mA
IO Power Supply
Reset output 1s / uF 10n = 10ms delay from power good to reset de-asserted.
Output voltage limited to 5.5V for input voltages up to 10.5V; output switches off at higher input voltages.

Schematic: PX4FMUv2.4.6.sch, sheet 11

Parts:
C1101, C1102, C1103: 22u/25V; 0805-CAP; PARTNO CL21A226MAQNNNE
C1104: 100u; 1206-CAP; PARTNO C3216X5R1A107M160AC
C1105, C1106, C1107: 0u1; 0402-CAP; PARTNO C1005X7R1E104K050BB
C1108, C1109, C1110: 10p/25V; 0402-CAP; PARTNO C0402C100J3GACTU
J601: DF13C-6P-1.25V; PARTNO DF13C-6P-1.25V(20)
L1101, L1102: KNH16C104DA5TS; KYOCERA-KNH16-DA; PARTNO KNH16C104DA5TS
R1101, R1102: 10K/0.1%; 0402-RES; PARTNO ERA-2AEB103X
R1103, R1104: 1M; 0402-RES; PARTNO RC0402FR-071ML
R1105, R1109, R1112: 453K; 0402-RES; PARTNO RMCF0402FT453K
R1106, R1110, R1113: 56K; 0402-RES; PARTNO ERA-2AEB563X
R1107, R1111, R1114: 105K; 0402-RES; PARTNO ERJ-2RKF1053X
R1115: 0R; 0402-RES; PARTNO ERJ-2GE0R00X
RN1101: 1M; EXB28V; PARTNO EXB-28V105JX
U1101: LTC4417; MO-220; PARTNO LTC4417IUF#PBF
U1102, U1103, U1104: NTHD4102PT1G; 1206-8; PARTNO NTHD4102PT1G

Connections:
!VBUS_VALID: RN1101.2 (1), U1101.P$9 (!VALID3); also elsewhere on the board
!VDD_BRICK_VALID: RN1101.4 (1), U1101.P$7 (!VALID1); also elsewhere on the board
!VDD_SERVO_VALID: RN1101.3 (1), U1101.P$8 (!VALID2); also elsewhere on the board
BATT_CURRENT_SENS: R1101.P$1 (1); also elsewhere on the board
BATT_CURRENT_SENS_PROT: J601.3, L1101.P$1, R1104.P$1 (1)
BATT_VOLTAGE_SENS: R1102.P$1 (1); also elsewhere on the board
BATT_VOLTAGE_SENS_PROT: J601.4, L1102.P$1, R1103.P$1 (1)
GND: C1101.P$2 (2), C1102.P$2 (2), C1103.P$2 (2), C1104.P$2 (2), C1105.P$2 (2), C1106.P$2 (2), C1107.P$2 (2), C1108.P$2 (2), C1109.P$2 (2), C1110.P$2 (2), J601.5, J601.6, L1101.P$3, L1101.P$4, L1101.P$5, L1102.P$3, L1102.P$4, L1102.P$5, R1103.P$2 (2), R1104.P$2 (2), R1107.P$2 (2), R1111.P$2 (2), R1114.P$2 (2), R1115.P$1 (1), U1101.P$10 (GND), U1101.P$25 (GND); also elsewhere on the board
unnamed: C1108.P$1 (1), R1105.P$2 (2), R1106.P$1 (1), U1101.P$1 (UV1)
unnamed: R1106.P$2 (2), R1107.P$1 (1), U1101.P$2 (OV1)
unnamed: C1109.P$1 (1), R1109.P$2 (2), R1110.P$1 (1), U1101.P$3 (UV2)
unnamed: R1110.P$2 (2), R1111.P$1 (1), U1101.P$4 (OV2)
unnamed: R1113.P$2 (2), R1114.P$1 (1), U1101.P$6 (OV3)
unnamed: C1110.P$1 (1), R1112.P$2 (2), R1113.P$1 (1), U1101.P$5 (UV3)
unnamed: C1105.P$1 (1), U1101.P$18 (VS1), U1102.P$1 (S), U1102.P$3 (S)
unnamed: L1102.P$2, R1102.P$2 (2)
unnamed: L1101.P$2, R1101.P$2 (2)
unnamed: R1115.P$2 (2), U1101.P$24 (HYS)
unnamed: C1106.P$1 (1), U1101.P$16 (VS2), U1103.P$1 (S), U1103.P$3 (S)
unnamed: C1107.P$1 (1), U1101.P$14 (VS3), U1104.P$1 (S), U1104.P$3 (S)
unnamed: U1101.P$13 (G3), U1104.P$2 (G), U1104.P$4 (G)
unnamed: U1101.P$15 (G2), U1103.P$2 (G), U1103.P$4 (G)
unnamed: U1101.P$17 (G1), U1102.P$2 (G), U1102.P$4 (G)
VBUS: C1103.P$1 (1), R1112.P$1 (1), U1101.P$19 (V3), U1104.P$7 (D), U1104.P$8 (D); also elsewhere on the board
VDD_5V_BRICK: C1101.P$1 (1), J601.1, J601.2, R1105.P$1 (1), U1101.P$21 (V1), U1102.P$7 (D), U1102.P$8 (D); also elsewhere on the board
VDD_5V_IN: C1104.P$1 (1), RN1101.5 (2), RN1101.6 (2), RN1101.7 (2), U1101.P$12 (VOUT), U1102.P$5 (D), U1102.P$6 (D), U1103.P$5 (D), U1103.P$6 (D), U1104.P$5 (D), U1104.P$6 (D); also elsewhere on the board
VDD_SERVO: C1102.P$1 (1), R1109.P$1 (1), U1101.P$20 (V2), U1103.P$7 (D), U1103.P$8 (D); also elsewhere on the board

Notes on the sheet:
Power source selector
Resistors picked so that undervoltage lockout starts at 4.0V and overvoltage lockout at 5.75V. Use 1% or better accuracy!
POWER PATH CONTROLLER: Does enable output if valid for continous 256 ms
XXX Check all input pins are 5V tolerant. Hooking this up to a 3.3V rail would make the lines non-readable during power-up sequencing

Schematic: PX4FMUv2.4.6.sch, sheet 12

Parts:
!VBUS_VALID: PAD.04; PAD.04X.04; PARTNO *
!VDD_BRICK_VALID: PAD.04; PAD.04X.04; PARTNO *
!VDD_SERVO_VALID: PAD.04; PAD.04X.04; PARTNO *
ADC_PR: PAD.04; PAD.04X.04; PARTNO *
CAN_H: PAD.04; PAD.04X.04; PARTNO *
CAN_L: PAD.04; PAD.04X.04; PARTNO *
FMU-BOOT1101: PAD.04; PAD.04X.04; PARTNO *
GND, GND.: PAD.04; PAD.04X.04; PARTNO *
IO-BOOT1101: PAD.04; PAD.04X.04; PARTNO *
JP1, JP2: FIDUCIAL1.5X3; FIDUCIAL-1.5X3; PARTNO *
M3_MOUNT1101, M3_MOUNT1102, M3_MOUNT1103, M3_MOUNT1104: MOUNT-HOLE3.1MM; MOUNT-HOLE3.1; PARTNO *
OSHW_LOGO: OSHW-LOGOS; OSHW-LOGO-S; PARTNO *
S1RX, S1TX, S2RX, S2TX, S3RX, S3TX, S4RX, S4TX, S5_RX, S5_TX: PAD.04; PAD.04X.04; PARTNO *
VBUS: PAD.04; PAD.04X.04; PARTNO *
VDDA_3V1101: PAD.04; PAD.04X.04; PARTNO *
VDD_3V1101, VDD_5V_BRICK, VDD_5V_IN: PAD.04; PAD.04X.04; PARTNO *
VDD_SERVO: PAD.04; PAD.04X.04; PARTNO *

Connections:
!VBUS_VALID: !VBUS_VALID.P$1; also elsewhere on the board
!VDD_BRICK_VALID: !VDD_BRICK_VALID.P$1; also elsewhere on the board
!VDD_SERVO_VALID: !VDD_SERVO_VALID.P$1; also elsewhere on the board
CAN_H: CAN_H.P$1; also elsewhere on the board
CAN_L: CAN_L.P$1; also elsewhere on the board
FMU-BOOT0: FMU-BOOT1101.P$1; also elsewhere on the board
FMU-VDD_3V3: VDD_3V1101.P$1; also elsewhere on the board
GND: GND.P$1, GND..P$1; also elsewhere on the board
IO-BOOT0: IO-BOOT1101.P$1; also elsewhere on the board
PRESSURE_SENS_IN: ADC_PR.P$1; also elsewhere on the board
SERIAL1_RX: S1RX.P$1; also elsewhere on the board
SERIAL1_TX: S1TX.P$1; also elsewhere on the board
SERIAL2_RX: S2RX.P$1; also elsewhere on the board
SERIAL2_TX: S2TX.P$1; also elsewhere on the board
SERIAL3_RX: S3RX.P$1; also elsewhere on the board
SERIAL3_TX: S3TX.P$1; also elsewhere on the board
SERIAL4_RX: S4RX.P$1; also elsewhere on the board
SERIAL4_TX: S4TX.P$1; also elsewhere on the board
SERIAL5_RX: S5_RX.P$1; also elsewhere on the board
SERIAL5_TX: S5_TX.P$1; also elsewhere on the board
VBUS: VBUS.P$1; also elsewhere on the board
VDD_3V3_SENSORS: VDDA_3V1101.P$1; also elsewhere on the board
VDD_5V_BRICK: VDD_5V_BRICK.P$1; also elsewhere on the board
VDD_5V_IN: VDD_5V_IN.P$1; also elsewhere on the board
VDD_SERVO: VDD_SERVO.P$1; also elsewhere on the board

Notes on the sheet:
Mounting holes to suit M3 fastener
and Richco R908 series spacer.
Use R908-5 spacers to stack with
other PX4 series boards (7.95 mm).
Production Testing Pads
Test and Fiducials
Minimum drill: 0.3 mm
Minimum trace width (use mm for traces): 0.15 mm
Minimum copper distance (all signals): 0.15 mm
Dimension / hole minimum distance: 0.2 mm
Layout grid: 4 mil, part grid: 4 mil. Dimensions / hole positions: 0.5 mm
Board: FR4 black, 1.0 mm. Solder stop on vias < 0.6 mm.
Signoff rules: Footprint checked, pinmap checked, schematic checked, cross-references to other pages checked.
Routing: 1: general/escape 2: ground 3: horizontal 4: vertical 5: power 6: general/escape
Fiducials for machine vision alignment.
Parts: Resistors: 0402 / 1% unless specified otherwise Capacitors: 0402 to 1206, ceramic, voltage rating: 10V unless specified
COMMS
POWER
STATUS AND ANALOG



Board: 6 copper layers, 70.0 x 40.5 mm, 290 parts (45 on the bottom side), 260 nets.

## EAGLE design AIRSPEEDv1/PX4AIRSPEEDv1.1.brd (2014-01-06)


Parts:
C1: 2u2; 0603-CAP; PARTNO C1608X6S1C225K080AC
J1: DF13-4P-1.25H; DF13A-4P-1.25H; PARTNO DF13-4P-1.25H(20)
JP1, JP2: FIDUCIAL1X2; FIDUCIAL-1X2; PARTNO *
JP3: 0R / DO NOT PLACE; SJ_3_0603_PASTE1&2; PARTNO *
L1: BKP1005HS121-T; 0402-IND; PARTNO BKP1005HS121-T
TP1, TP2, TP3, TP4: TPTP15R; TP15R; PARTNO *
U1: 4525DO-DS5AI001DP; PARTNO 4525DO-DS5AI001DP
U$2, U$4: MOUNT-HOLE3.1MM; MOUNT-HOLE3.1; PARTNO *

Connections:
GND: C1.P$2 (2), J1.4, JP3.1, TP4.TP, U1.1 (GND)
unnamed: J1.2, TP2.TP, U1.4 (SCL/SCLK)
unnamed: J1.3, TP3.TP, U1.3 (SDA/MISO)
unnamed: J1.1, L1.P$2 (2), TP1.TP
unnamed: JP3.2, U1.5 (INT/SS)
VCC_5V: C1.P$1 (1), JP3.3, L1.P$1 (1), U1.2 (VCC)

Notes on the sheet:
Sensors



Board: 4 copper layers, 16.0 x 23.0 mm, 13 parts (4 on the bottom side), 6 nets.

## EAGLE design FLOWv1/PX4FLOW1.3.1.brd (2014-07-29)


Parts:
!RESET: PAD.04; PAD.04X.04; PARTNO *
ADDR0, ADDR1, ADDR2: JUMPER-2; SJ_2; PARTNO *
BOOT1: PAD.04; PAD.04X.04; PARTNO *
C3, C4: 8p; 0402-CAP
D1: MSS1P4-M3; MICROSMP; PARTNO MSS1P4-M3/89A
IC1: STM32F4X7VX; TQFP100; PARTNO STM32F407VGT6
J1: DF13-4P-1.25H; DF13A-4P-1.25H; PARTNO DF13A-4P-1.25H(20)
J2, J3: DF13-6P-1.25H; DF13A-6P-1.25H; PARTNO DF13A-6P-1.25H(20)
J4: MB1040; MAXSONAR; PARTNO *
J5: 47346-0001; MOLEX-47346-0001; PARTNO 47346-0001
J6: ARM_MINI_JTAG; FTSH-105-01-XXX-DV-K; PARTNO M50-3900542
JP2: JUMPER-2; SJ_2; PARTNO *
L1, L2, L8: FERRITE; 0402-IND; PARTNO BKP1005HS121-T
OTG_DM: PAD.04; PAD.04X.04; PARTNO *
OTG_DP: PAD.04; PAD.04X.04; PARTNO *
R1, R2: 1k5; 0402-RES
R3, R4: 100; 0402-RES; PARTNO RMCF0402JT100R
R5: 10K; 0402-RES; PARTNO RMCF0402FT10K0
R6, R8: 22R; 0402-RES; PARTNO RMCF0402JT22R0
R7: 10k; 0402-RES; PARTNO MFR-25FBF-10K0
R10: 1k; 0402-RES; PARTNO RMCF0402JT1K00
R11: 0R; 0402-RES; PARTNO RMCF0402JT1K00
U$10: OSHW-LOGOS; OSHW-LOGO-S; PARTNO *
USART2_RX, USART2_TX, USART3_RX, USART3_TX: PAD.04; PAD.04X.04; PARTNO *
USB_VBUS: PAD.04; PAD.04X.04; PARTNO *
VDD_3V3, VDD_3V3_ANALOG, VDD_5V, VDD_5V_IN: PAD.04; PAD.04X.04; PARTNO *
X1: 24.000 KHz 3.2x2.5mm 8-10pf; OSCILLATOR-3.2X2.5; PARTNO NX3225SA-24.000000MHZ

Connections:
!JTRST: IC1.90 (PB4), J6.10
!RESET: !RESET.P$1; also elsewhere on the board
ADC12_IN4: IC1.33 (PC4)
ADC12_IN5: IC1.34 (PC5)
ADC123_IN10: IC1.15 (PC0), J4.AN
ADC123_IN11: IC1.16 (PC1)
ADC123_IN12: IC1.17 (PC2)
ADC123_IN13: IC1.18 (PC3)
ADDR0: ADDR0.2, IC1.7 (PC13)
ADDR1: ADDR1.2, IC1.8 (PC14)
ADDR2: ADDR2.2, IC1.9 (PC15)
CAM_NRESET: IC1.30 (PA5); also elsewhere on the board
CAN1_RX: IC1.81 (PD0)
CAN1_TX: IC1.82 (PD1)
DCMI_D0: IC1.63 (PC6); also elsewhere on the board
DCMI_D1: IC1.64 (PC7); also elsewhere on the board
DCMI_D2: IC1.97 (PE0); also elsewhere on the board
DCMI_D3: IC1.98 (PE1); also elsewhere on the board
DCMI_D4: IC1.3 (PE4); also elsewhere on the board
DCMI_D5: IC1.92 (PB6); also elsewhere on the board
DCMI_D6: IC1.4 (PE5); also elsewhere on the board
DCMI_D7: IC1.5 (PE6); also elsewhere on the board
DCMI_D8: IC1.78 (PC10); also elsewhere on the board
DCMI_D9: IC1.80 (PC12); also elsewhere on the board
DCMI_D10: IC1.91 (PB5)
DCMI_D11_UART5_RX: IC1.83 (PD2)
DCMI_HSYNC: IC1.29 (PA4); also elsewhere on the board
DCMI_PIXCK: IC1.31 (PA6); also elsewhere on the board
DCMI_VSYNC: IC1.93 (PB7); also elsewhere on the board
GND: ADDR0.1, ADDR1.1, ADDR2.1, C3.P$2 (2), C4.P$1 (1), IC1.44 (PE13), IC1.45 (PE14), IC1.46 (PE15), J1.4, J2.6, J3.6, J4.GND, J5.GND (5), J5.GND1, J5.GND2, J5.GND3, J5.GND4, J6.3, J6.5, J6.9, R5.2, X1.2 (NC_2), X1.4 (NC_4); also elsewhere on the board
I2C1_SCL: IC1.95 (PB8), R3.1
I2C1_SCL_EXT: J1.2, R3.2
I2C1_SDA: IC1.96 (PB9), R4.1
I2C1_SDA_EXT: J1.3, R4.2
I2C2_SCL: IC1.47 (PB10), R1.P$1 (1); also elsewhere on the board
I2C2_SDA: IC1.48 (PB11), R2.P$1 (1); also elsewhere on the board
I2C3_SCL---: IC1.67 (PA8)
JTCK-SWCLK: IC1.76 (PA14), J6.4
JTDI: IC1.77 (PA15), J6.8
JTDO: IC1.89 (PB3), J6.6
JTMS-SWDIO: IC1.72 (PA13), J6.2
LED_AMBER: IC1.1 (PE2); also elsewhere on the board
LED_BLUE: IC1.2 (PE3); also elsewhere on the board
LED_RED: IC1.38 (PE7); also elsewhere on the board
MAG_DRDY---: IC1.36 (PB1)
unnamed: C4.P$2 (2), IC1.13 (OSC_OUT), X1.1
unnamed: C3.P$1 (1), IC1.12 (OSC_IN), X1.3
unnamed: J1.1, L2.P$2 (2)
unnamed: J2.1, JP2.2
unnamed: D1.ANODE (A), L8.P$1 (1)
OTG_FS_ID: IC1.69 (PA10), R7.2
OTG_FS_N: IC1.70 (PA11), R6.2
OTG_FS_P: IC1.71 (PA12), R8.2
OTG_ID: J5.ID (4), R7.1
OTG_N: J5.D- (2), OTG_DM.P$1, R6.1
OTG_P: J5.D+ (3), OTG_DP.P$1, R8.1
PB2-BOOT1: BOOT1.P$1, IC1.37 (PB2), R5.1
PRES_DRDY---: IC1.35 (PB0)
SONAR_TX: J4.TX, R11.1
SPI1_MOSI---: IC1.32 (PA7)
SPI2_MISO: IC1.53 (PB14); also elsewhere on the board
SPI2_MOSI: IC1.54 (PB15); also elsewhere on the board
SPI2_NSS: IC1.51 (PB12); also elsewhere on the board
SPI2_SCK: IC1.52 (PB13); also elsewhere on the board
TIM1_CH1: IC1.40 (PE9)
TIM1_CH2: IC1.42 (PE11)
TIM4_CH2: IC1.60 (PD13), J4.PW
TIM4_CH3: IC1.61 (PD14)
TIM4_CH4: IC1.62 (PD15)
TIM5_CH1: IC1.23 (PA0)
TIM5_CH2: IC1.24 (PA1)
TIM5_CH3_EXPOSURE: IC1.25 (PA2); also elsewhere on the board
TIM5_CH4_STANDBY: IC1.26 (PA3); also elsewhere on the board
TIM8_CH3_MASTERCLOCK: IC1.65 (PC8); also elsewhere on the board
TIM8_CH4_LED_OUT: IC1.66 (PC9); also elsewhere on the board
UART4_RX: IC1.79 (PC11), R10.2, R11.2
USART2_CK: IC1.88 (PD7)
USART2_CTS: IC1.84 (PD3), J2.4
USART2_RTS: IC1.85 (PD4), J2.5
USART2_RX: IC1.87 (PD6), J2.3, USART2_RX.P$1
USART2_TX: IC1.86 (PD5), J2.2, USART2_TX.P$1
USART3_CK: IC1.57 (PD10)
USART3_CTS: IC1.58 (PD11), J3.5
USART3_RTS: IC1.59 (PD12), J3.4
USART3_RX: IC1.56 (PD9), J3.2, USART3_RX.P$1
USART3_TX: IC1.55 (PD8), J3.3, USART3_TX.P$1
US_EN1: IC1.39 (PE8), J4.RX
US_EN2: IC1.41 (PE10)
VBUS: IC1.68 (PA9), J5.VBUS (1), L8.P$2 (2), USB_VBUS.P$1
VDD_3V3: IC1.43 (PE12), J6.1, R1.P$2 (2), R2.P$2 (2), VDD_3V3.P$1; also elsewhere on the board
VDD_3V3_ANALOG: VDD_3V3_ANALOG.P$1; also elsewhere on the board
VDD_5V: D1.CATHODE (C), JP2.1, R10.1, VDD_5V.P$1; also elsewhere on the board
VDD_5V_IN: L1.P$1 (1), L2.P$1 (1); also elsewhere on the board
VDD_5V_IN_UART3: J3.1, L1.P$2 (2), VDD_5V_IN.P$1
VDD_SONAR: J4.VDD; also elsewhere on the board

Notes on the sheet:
Ports and Connectors
CPU Ports
I2C1
USB
JTAG
UART2 - MASTER, for radio modems
UART3 - SLAVE, for autopilot connection
SONAR
PRODUCTION TEST PADS


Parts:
BOOT0: PAD.05; PAD.05X.05; PARTNO *
C5, C7, C8, C9, C10, C15, C17, C23, C28, C29, C30, C31, C32: 0u1; 0402-CAP; PARTNO CC0402ZRY5V7BB104
C6, C27: 10u; EIA3216; PARTNO F931A106MAA
C11, C12: 2u2; 0402-CAP; PARTNO C1608Y5V1C225Z
C13: 470p; 0402-CAP; PARTNO CC0402KRX7R9BB471
C24: 10n; 0402-CAP; PARTNO CC0402ZRY5V7BB104
C26: 1n; 0402-CAP; PARTNO CC0402ZRY5V7BB104
IC1: STM32F4X7VX; TQFP100; PARTNO STM32F407VGT6
JP1: JUMPER-30603; SJ_3_0603_PASTE1&2; PARTNO RMCF0402ZT0R00
L11: FERRITE; 0402-IND; PARTNO BKP1005HS121-T
LED1: GREEN; LED-0603; PARTNO LNJ337W83RA
LED2: AMBER; LED-0603; PARTNO LNJ437W84RA
LED3: BLUE; LED-0603; PARTNO LNJ937W8CRA
LED4: RED; LED-0603; PARTNO LNJ237W82RA
Q1: NTGS4111P; TSOP-6; PARTNO NTGS4111P
R13, R14: 270R; 0402-RES; PARTNO MCR01MZPJ271
R15, R17: 270R; 0402-RES; PARTNO MCR01MZPJ820
R16, R18: 10K; 0402-RES; PARTNO RMCF0402FT10K0
S1: RESET; EVQP7J01K; PARTNO EVQP7J01K
U1: V_REG_LDOSMD; SOT23-5; PARTNO MIC5207-3.3YM5
U8: 128KB EEPROM; MSOP-8; PARTNO 24FC128-I/MS
U$1, U$2, U$3, U$4: MOUNT-HOLE3.1MM; MOUNT-HOLE3.1; PARTNO *

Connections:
!RESET: C17.2, IC1.14 (NRST), R16.1, S1.A1 (1); also elsewhere on the board
BOOT0: BOOT0.P$1, IC1.94 (BOOT0), R18.2
GND: C5.2, C6.C (-), C7.2, C8.2, C9.2, C10.2, C11.2, C12.2, C13.2, C15.2, C17.1, C23.2, C24.2, C26.2, C27.C (-), C28.2, C29.2, C30.2, C31.2, C32.2, IC1.10 (VSS), IC1.20 (VSSA), IC1.27 (VSS_4), IC1.74 (VSS), IC1.99 (VSS), Q1.3 (G), R13.1, R18.1, S1.B3 (2), U1.2 (GND), U8.1 (A0), U8.2 (A1), U8.3 (A2), U8.4 (VSS); also elsewhere on the board
I2C2_SCL: U8.6 (SCL); also elsewhere on the board
I2C2_SDA: U8.5 (SDA); also elsewhere on the board
LED_AMBER: R14.1; also elsewhere on the board
LED_BLUE: R15.1; also elsewhere on the board
LED_RED: R17.1; also elsewhere on the board
unnamed: C13.1, U1.4 (BP)
unnamed: LED4.C, R17.2
unnamed: LED3.C, R15.2
unnamed: LED1.C, R13.2
unnamed: LED2.C, R14.2
VCAP_1: C11.1, IC1.49 (VCAP_1)
VCAP_2: C12.1, IC1.73 (VCAP_2)
VDD_3V3: C5.1, C6.A (+), C8.1, C9.1, C10.1, C28.1, C29.1, C30.1, C31.1, C32.1, IC1.6 (VBAT), IC1.11 (VDD), IC1.19 (VDD), IC1.28 (VDD), IC1.50 (VDD), IC1.75 (VDD), IC1.100 (VDD), JP1.3, L11.P$1 (1), LED1.A, LED2.A, LED3.A, LED4.A, R16.2, U1.5 (OUT), U8.8 (VCC); also elsewhere on the board
VDD_3V3_ANALOG: C15.1, C23.1, C24.1, C26.1, IC1.21 (VREF+), IC1.22 (VDDA), L11.P$2 (2); also elsewhere on the board
VDD_5V: C7.1, C27.A (+), JP1.1, Q1.4 (S), U1.1 (IN), U1.3 (EN); also elsewhere on the board
VDD_5V_IN: Q1.1 (D), Q1.2 (D1), Q1.5 (D2), Q1.6 (D3); also elsewhere on the board
VDD_SONAR: JP1.2; also elsewhere on the board

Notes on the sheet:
Power and Reset
Microchip 24FC128-I/MS
Microchip 24AA256-I/MS
Mounting holes to suit M2.5 fastener
and Richco R907 series spacer.
ST Micro M24128-BWDW6TP
Reverse input protection
Mount either R21 or R23 to power Sonar with 5V or 3.3V
Bypass caps as close to device pins as possible.

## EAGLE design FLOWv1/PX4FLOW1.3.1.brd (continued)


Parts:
C1, C25: 0u01; 0402-CAP; PARTNO CC0402KRX7R7BB103
C2, C16, C18, C19, C20, C21, C22: 0u1; 0402-CAP; PARTNO CC0402ZRY5V7BB104
R9: 10k; 0402-RES; PARTNO MCR01MZPJ271
R19, R20: 1k; 0402-RES; PARTNO RMCF0402JT1K00
U12: L3GD20; L3G4200DH-MAN; PARTNO L3GD20
U$5: MT9V034; CLCC-48; PARTNO MT9V034C12STM
U$8: LENSMOUNT_M12; LENSMOUNT_LARGE_M12; PARTNO *

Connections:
CAM_NRESET: C1.1, R9.1, U$5.32 (!RESET); also elsewhere on the board
DCMI_D0: U$5.43 (DOUT2); also elsewhere on the board
DCMI_D1: U$5.42 (DOUT3); also elsewhere on the board
DCMI_D2: U$5.41 (DOUT4); also elsewhere on the board
DCMI_D3: U$5.15 (DOUT5); also elsewhere on the board
DCMI_D4: U$5.16 (DOUT6); also elsewhere on the board
DCMI_D5: U$5.17 (DOUT7); also elsewhere on the board
DCMI_D6: U$5.18 (DOUT8); also elsewhere on the board
DCMI_D7: U$5.19 (DOUT9); also elsewhere on the board
DCMI_D8: U$5.45 (DOUT0); also elsewhere on the board
DCMI_D9: U$5.44 (DOUT1); also elsewhere on the board
DCMI_HSYNC: U$5.20 (LINE_VALID); also elsewhere on the board
DCMI_PIXCK: U$5.46 (PIXCLK); also elsewhere on the board
DCMI_VSYNC: U$5.21 (FRAME_VALID); also elsewhere on the board
GND: C1.2, C2.2, C16.2, C18.2, C19.2, C20.2, C21.2, C22.2, C25.2, U12.8 (RES_P8_GND), U12.9 (RES_P9_GND), U12.10 (RES_P10_GND), U12.11 (RES_P11_VDD), U12.12 (RES_P12_GND), U12.13 (GND), U$5.7 (LVDS_GND), U$5.9 (BYPASS_CLKIN_P), U$5.11 (SER_DATAIN_P), U$5.12 (LVDS_GND), U$5.13 (DGND), U$5.29 (RSVD), U$5.34 (AGND), U$5.38 (AGND), U$5.48 (DGND); also elsewhere on the board
I2C2_SCL: U$5.25 (SCLK); also elsewhere on the board
I2C2_SDA: U$5.24 (SDATA); also elsewhere on the board
unnamed: R19.1, U$5.8 (BYPASS_CLKIN_N)
unnamed: R20.1, U$5.10 (SER_DATAIN_N)
unnamed: C25.1, U12.14 (PLLFILT)
SPI2_MISO: U12.4 (SDO/SA0); also elsewhere on the board
SPI2_MOSI: U12.3 (SDA/SDI/SDO); also elsewhere on the board
SPI2_NSS: U12.5 (CS); also elsewhere on the board
SPI2_SCK: U12.2 (SCL/SPC); also elsewhere on the board
TIM5_CH3_EXPOSURE: U$5.23 (EXPOSURE); also elsewhere on the board
TIM5_CH4_STANDBY: U$5.33 (STANDBY); also elsewhere on the board
TIM8_CH3_MASTERCLOCK: U$5.47 (SYSCLK); also elsewhere on the board
TIM8_CH4_LED_OUT: U$5.27 (LED_OUT); also elsewhere on the board
VDD_3V3: C2.1, C16.1, C18.1, R9.2, R19.2, R20.2, U12.1 (VDD_IO), U$5.1 (VDD), U$5.6 (VDD_LVDS), U$5.14 (VDD), U$5.28 (OE), U$5.30 (SCTRL_ADR0), U$5.31 (SCTRL_ADR1); also elsewhere on the board
VDD_3V3_ANALOG: C19.1, C20.1, C21.1, C22.1, U12.15 (RES_P15_VDD), U12.16 (VDD), U$5.35 (VAA), U$5.39 (VAA), U$5.40 (VAA_PIX); also elsewhere on the board

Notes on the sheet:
Sensors
Bypass caps as close to device pins as possible.
NOTE: Stuff C1 & C2 with 0R0 for STM32F1xx series device.



Board: 4 copper layers, 35.0 x 45.4 mm, 98 parts (22 on the bottom side), 84 nets.

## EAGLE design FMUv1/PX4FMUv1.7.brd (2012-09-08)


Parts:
!JTRST: PAD.04; PAD.04X.04; PARTNO *
!RESET: PAD.04; PAD.04X.04; PARTNO *
C1, C2, C5: 0u1; 0402-CAP; PARTNO CC0402ZRY5V7BB104
C3, C4: 8p; 0402-CAP; PARTNO C1005C0G1H080C
D1: MSS1P4-M3; MICROSMP; PARTNO MSS1P4-M3/89A
F1: 500mA; 0402-PTC; PARTNO MF-FSMF050X-2
F2: 200mA; 0402-PTC; PARTNO MF-FSMF020X-2
I2C1_SCL_MOTOR, I2C1_SDA_MOTOR, I2C2_SCL: PAD.03; PAD.03X.03; PARTNO *
I2C2_SDA: PAD.04; PAD.04X.04; PARTNO *
J1: DF13-15P-1.25H; DF13A-15P-1.25H; PARTNO DF13A-15P-1.25H(20)
J2: HEADER_2X15-REV; HEADER_2MM_2X15_REVERSE; PARTNO 953230-2000-AR-PR
J3: HEADER_2X15; HEADER_2MM_2X15; PARTNO 953230-2000-AR-PR
J4: DF13-5P-1.25H; DF13A-5P-1.25H; PARTNO DF13A-5P-1.25H(20)
J5: 47346-0001; MOLEX-47346-0001; PARTNO 47346-0001
J6: ARM_MINI_JTAG-TH; FTSH-105-01-XXX-DV; PARTNO M50-3900542
JP1, JP2: 0R; SJ_3_0603_PASTE1&2; PARTNO RMCF0402ZT0R00
JTCK-SWCLK: PAD.04; PAD.04X.04; PARTNO *
JTDI: PAD.04; PAD.04X.04; PARTNO *
JTDO: PAD.04; PAD.04X.04; PARTNO *
JTMS-SWDIO: PAD.04; PAD.04X.04; PARTNO *
L1, L2, L3, L8: FERRITE; 0402-IND; PARTNO BKP1005HS121-T
L4, L5, L10: BLM15HD102SN1; 0402-IND; PARTNO BLM15HD102SN1
Q2: NTGS4111P; TSOP-6; PARTNO NTGS4111P
R1, R2, R7, R9: 1K5; 0402-RES; PARTNO RMCF0402JT1K50
R3, R4: 100; 0402-RES; PARTNO RMCF0402JT100R
R5, R21, R23: 10K; 0402-RES; PARTNO RMCF0402FT10K0
R6, R8: 22R; 0402-RES; PARTNO RMCF0402JT22R0
R10: 1K0; 0402-RES; PARTNO RMCF0402JT1K00
R11: 47K/0.1%; 0402-RES; PARTNO ERA-2AEB473X
R12: 10K/0.1%; 0402-RES; PARTNO ERA-2AEB103X
RN1: CTS742C083; PARTNO TC164-JR-07100RL
SPI1_MISO, SPI1_MOSI, SPI1_SCK: PAD.04; PAD.04X.04; PARTNO *
U1: STM32F405RGT6; TQFP64; PARTNO STM32F405RGT6
U2, U3, U4: TXS0102DCUR; TI-DCU; PARTNO TXS0102DCUR
U5: SN74LVC2T45; TI-DCU; PARTNO SN74LVC2T45
U13: AMP 114-00841-68; AMPHENOL_114-00841-68; PARTNO 114-00841-68
U$7: OSHW-LOGOS; OSHW-LOGO-S; PARTNO *
USART6_RX, USART6_TX: PAD.04; PAD.04X.04; PARTNO *
VDDA_3V3: PAD.04; PAD.04X.04; PARTNO *
VDD_3V3: PAD.04; PAD.04X.04; PARTNO *
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

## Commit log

2012-09-08 Initial import
    [PX4FMUv1.6.brd, PX4FMUv1.6.sch, PX4FMUv1.7.brd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]
2013-01-30 Release files for PX4FMU v1.7.1
    [PX4FMUv1.7.1.brd, PX4FMUv1.7.1.sch]
2013-10-09 FMU v2.3 release, as the HW is now shipping to customers of Iris
    [PX4FMUv2.3.brd, PX4FMUv2.3.sch]
2013-10-25 Updates to reflect questions asked on mailing list https://groups.google.com/forum/#!topicsearchin/px4users/mosfet%7Csort:date/px4users/fcfwdMKPhbI
    [PX4FMUv2.3.brd, PX4FMUv2.3.sch]
2014-01-02 Checking in FMU v2.4, as it ships now
    [A_PX4_PARTS_DATABASE.csv, PX4FMUv2.4.brd, PX4FMUv2.4.sch]
2014-01-02 Added final sub-rev now shipping
    [PX4FMUv2.4.3.brd, PX4FMUv2.4.3.sch]
2014-01-06 Airspeed sensing
    [A_PX4_PARTS_DATABASE.csv, PX4AIRSPEEDv1.1.brd, PX4AIRSPEEDv1.1.sch]
2014-03-04 Added flow sensor
    [PX4FLOW1.3.1.brd, PX4FLOW1.3.1.sch]
2014-05-27 FMU v2.4.5 published - changes values of C1108 / C1109 / C1110 to 10p/25V. NO SCHEMATIC OR BOARD CHANGES.
    [PX4FMUv2.4.5.brd, PX4FMUv2.4.5.sch]
2014-07-29 Check in WIP 2.4.6 design. Robustified against misbehaving RC receivers (excessive current, reverse overvoltage)
    [PX4FMUv2.4.6.brd, PX4FMUv2.4.6.sch]
2014-11-26 FMU v2.4.5 sch mistake fix - C1110 to 10p
    [PX4FMUv2.4.5.brd, PX4FMUv2.4.5.sch]
2015-06-06 Import Pixhawk 2 / FMUv3 design files
    [80PIN_FMU3_REV_C.SchDoc, Bill of Materials-FMU3_REV_D(FMU3_REV_D).xlsx, Bill of Materials-PSM_REV_C(PCA_0007_PSM).xlsx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]
2015-11-24 Move PX4 IOv1 boards to their own folder
    [PX4IOARMTv1.0.brd, PX4IOARMTv1.0.sch, PX4IOARv1.2.brd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]
2015-11-24 Move FMUv1 to its own folder
    [PX4FMUv1.6.brd, PX4FMUv1.6.sch, PX4FMUv1.7.1.brd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]
2015-11-24 Move FLOW to its own folder
    [PX4FLOW1.3.1.brd, PX4FLOW1.3.1.sch]
2015-11-24 Move airspeed to its own folder
    [PX4AIRSPEEDv1.1.brd, PX4AIRSPEEDv1.1.sch]
2015-11-24 Remove unfinished 2.4.6 rev
    [PX4FMUv2.4.6.brd, PX4FMUv2.4.6.sch]
2015-11-24 Move FMUv2 boards to their own folder
    [PX4FMUv2.3.brd, PX4FMUv2.3.sch, PX4FMUv2.4.3.brd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]
2015-11-27 px4fmu 2.4.6 initial commit: Q601 and R620 deleted, R621=220R from VDD_3V3_SENSORS to GND
    [PX4FMUv2.4.6.brd, PX4FMUv2.4.6.sch]
2016-05-06 Add MindPXv2 hardware
    [MindPX2.2.SchDoc, imu.SchDoc]
2016-10-20 Sapog HW - initial commit
    [sapog_reference_hardware.brd, sapog_reference_hardware.sch]
2016-10-31 Add new MindPX v2.8 and MindRacer V1.2 hardware
    [MINDRACER-V12.DSN, MindPX V2.8 SCH.SchDoc]
2016-11-15 Updated description of the Sapog ESC hardware
2018-04-03 Fixed the BOM entry of the power decoupling capacitor. 25 V tantalum capacitors degrade quickly, the new recommendation is to use 35 V rated capacitors. For more info, see https://forum.zubax.com/t/c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
    [sapog_reference_hardware.sch]
2022-05-16 add altium source file for PRI breakout board
    [830-00011 Microhard Module Breakout Board.GBL, 830-00011 Microhard Module Breakout Board.GBO, 830-00011 Microhard Module Breakout Board.GBS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]
2022-05-18 Release Pixhawk Debug Adapter (#110)
    [01_cover_page.SchDoc, 02_main.SchDoc, Bill of Materials-pixhawk_debug_adapter_mini(Production).xlsx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]

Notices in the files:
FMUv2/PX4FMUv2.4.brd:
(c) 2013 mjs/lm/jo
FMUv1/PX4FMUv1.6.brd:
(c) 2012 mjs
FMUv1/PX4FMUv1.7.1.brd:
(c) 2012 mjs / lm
